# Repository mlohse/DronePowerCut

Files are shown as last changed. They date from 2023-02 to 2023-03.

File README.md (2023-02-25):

# DronePowerCut

This board is supposed to be connected between the main battery and the flight controller of a drone/opto-copter and provides an emergency power-off in case the drone get's out of control.
The board has been designed for 6s LiPo batteries (22.2V) and can handle continuous currents of up to 80A.

# Bill of Material (BOM)
The PCB can be ordered at OSH Park (they ship worldwide):

* https://oshpark.com/shared_projects/SKaDHxAu (rev.A)

It doesn't really matter of which brand/type you order resistors and capacitors, nor does this board require any tight tolerances. You can purchase whatever your local hardware dealer has on stock fitting the value/package described by the schematic.
However, for convenience I've created a virtual shopping basket at Reichelt Elektronik:

* https://www.reichelt.de/my/2021258

MosFETs and Voltage regulator are available at Farnell:

* https://de.farnell.com/infineon/auirfs8409-7trl/mosfet-n-kanal-40v-240a-to-263/dp/2839427?st=auirfs8409
* https://de.farnell.com/microchip/mic5219-3-6ym5-tr/ldo-0-5vdo-0-5a-3-6v-1-5sot23/dp/2510256?st=mic5219

# Building and Flashing the Firmware
You need to have an AVR toolchain installed (make, gcc, binutils)

On Arch Linux simply install the following packages:

`# pacman -S community/avr-gcc community/avr-binutils community/avr-libc`

You may likely want to install avrdude (of course if your programmer requires a different software you can skip this step):

`# pacman -S avrdude`

Please don't forget to adapt the `PROGRAMMER`/`PORT` section in the `Makefile` according to your programmer.

To build the firmware change into the `src` directory and run:

`# make`

...then connect the board to your ISP programmer - the boards needs to be powered (consumes < 50mA) through the programmer - and flash the firmware:

`# make program`

**Optional**: It shouldn't be necessary to flash fuses, as they are left to defaults. But in case the MCU behaves weird in any way...

`# make fuses`

Done.

# LED States (Debugging)

## Power LED (blue)
This led should always be flashing with 1Hz during opartion. If constantly lid or off the MCU has crashed - should never happen of course ;)

## Activity LED (green)
This led indicated whether there is a signal from the receiver:

* **off**: no signal
* **flashing with 5Hz**: invalid signal (pulse to short/long, see `CTRL_DECODER_VAL_MIN`/`CTRL_DECODER_VAL_MAX`)
* **constantly lid**: signal ok (during normal operation this should always be the case)

## OFF LED (red)
This led indicates when lid that power has been cut (emergency off active).

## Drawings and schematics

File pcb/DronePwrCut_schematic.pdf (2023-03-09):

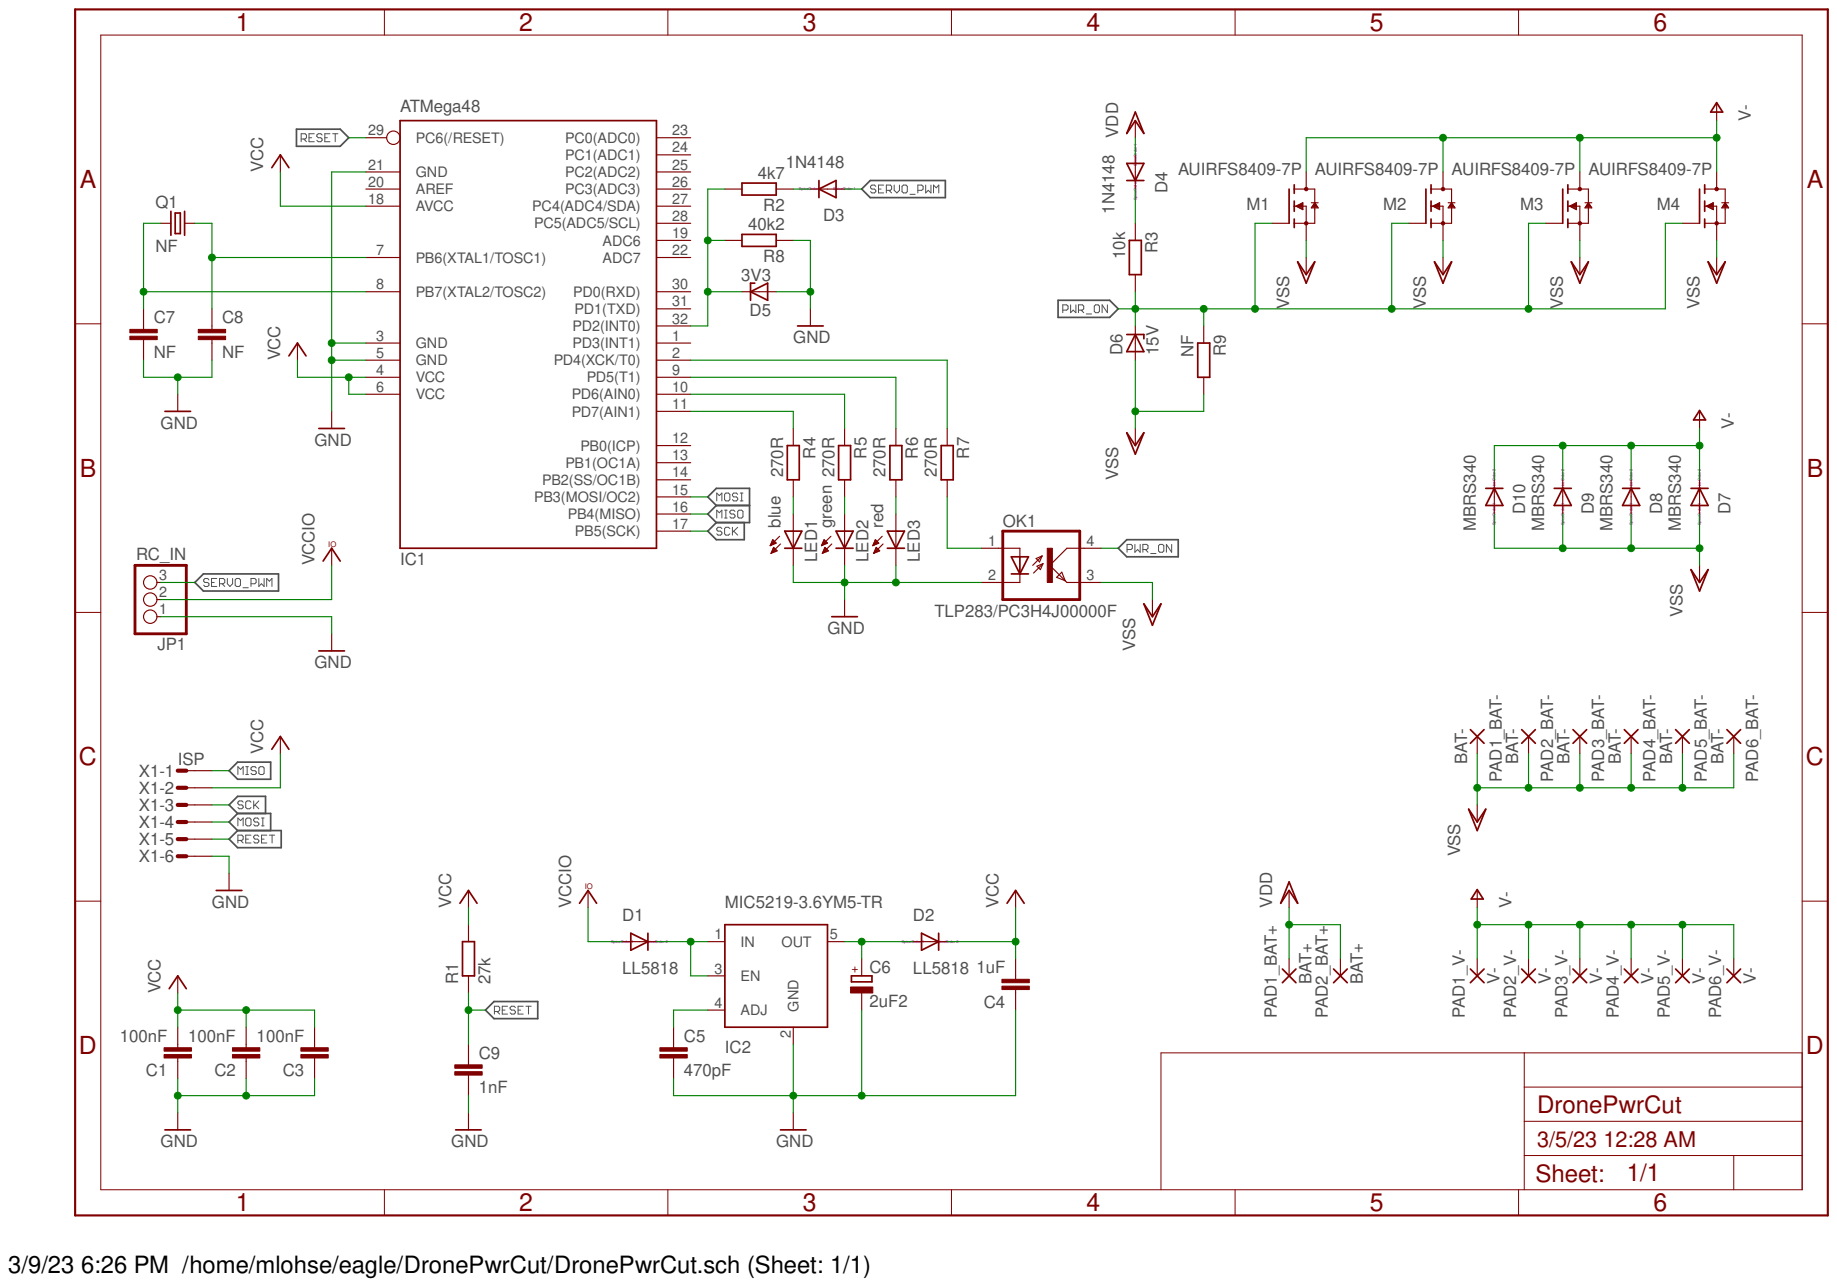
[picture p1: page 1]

BAT- BAT-

3/9/23 6:26 PM /home/mlohse/eagle/DronePwrCut/DronePwrCut.sch (Sheet: 1/1)

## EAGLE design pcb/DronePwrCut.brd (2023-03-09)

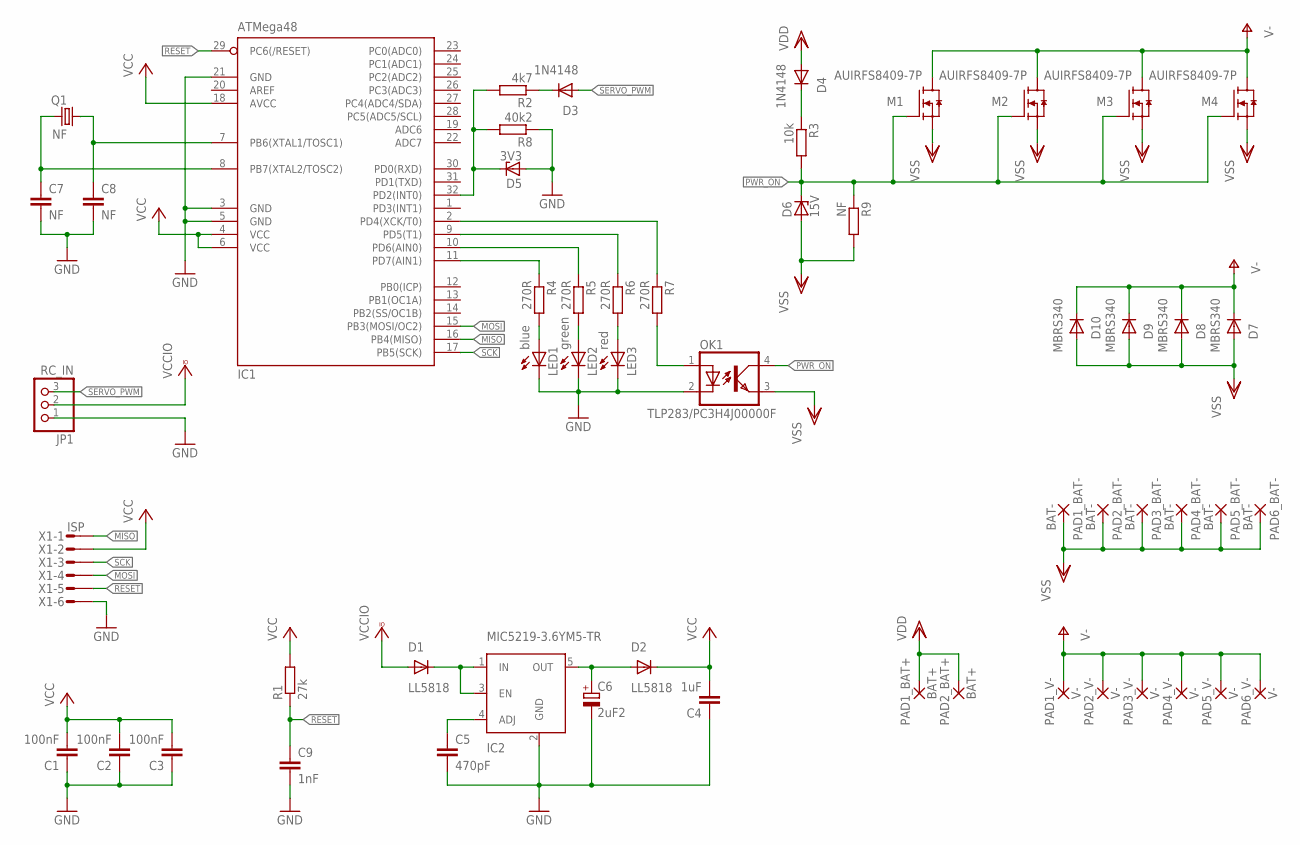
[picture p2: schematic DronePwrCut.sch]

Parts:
C1, C2, C3: 100nF; C1206K
C4: 1uF; C1206K
C5: 470pF; C1206K
C6: 2uF2; SMC_B
C7, C8: NF; C1206K
C9: 1nF; C1206K
D1, D2: LL5818; MELF-MLL41
D3, D4: 1N4148; SOD80C
D5: 3V3; SOD80C
D6: 15V; SOD80C
D7, D8, D9, D10: MBRS340; SMC
IC1: ATMega48; TQFP32-08
IC2: MIC5219-3.6YM5-TR; SOT23-5
JP1: RC_IN; 1X03
LED1: blue; CHIPLED_1206
LED2: green; CHIPLED_1206
LED3: red; CHIPLED_1206
M1, M2, M3, M4: AUIRFS8409-7P; P-TO263-7-1
OK1: TLP283/PC3H4J00000F; MINI-FLAT-4
PAD1_BAT+, PAD2_BAT+: BAT+; 1,6/0,8
PAD1_BAT-, PAD2_BAT-, PAD3_BAT-, PAD4_BAT-, PAD5_BAT-, PAD6_BAT-: BAT-; 1,6/0,8
PAD1_V-, PAD2_V-, PAD3_V-, PAD4_V-, PAD5_V-, PAD6_V-: V-; 1,6/0,8
Q1: NF; HC49UP
R1: 27k; R1206
R2: 4k7; R1206
R3: 10k; R1206
R4, R5, R6, R7: 270R; R1206
R8: 40k2; R1206
R9: NF; R1206
X1: ISP; MICROMATCH-6

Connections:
GND: C1.1, C2.1, C3.1, C4.1, C5.2, C6.-, C7.2, C8.2, C9.2, D5.A, IC1.3 (GND), IC1.5 (GND), IC1.21 (GND), IC2.2 (GND), JP1.1, LED1.C, LED2.C, LED3.C, OK1.2 (C), R8.1, X1.6
MISO: IC1.16 (PB4(MISO)), X1.1
MOSI: IC1.15 (PB3(MOSI/OC2)), X1.4
unnamed: C8.1, IC1.7 (PB6(XTAL1/TOSC1)), Q1.1
unnamed: C6.+, D2.A, IC2.5 (OUT)
unnamed: C5.1, IC2.4 (ADJ)
unnamed: D1.C, IC2.1 (IN), IC2.3 (EN)
unnamed: C7.1, IC1.8 (PB7(XTAL2/TOSC2)), Q1.2
unnamed: D5.C, IC1.32 (PD2(INT0)), R2.2, R8.2
unnamed: D3.C, R2.1
unnamed: D4.C, R3.1
unnamed: IC1.11 (PD7(AIN1)), R4.1
unnamed: IC1.10 (PD6(AIN0)), R5.1
unnamed: IC1.9 (PD5(T1)), R6.1
unnamed: IC1.2 (PD4(XCK/T0)), R7.1
unnamed: LED1.A, R4.2
unnamed: LED2.A, R5.2
unnamed: LED3.A, R6.2
unnamed: OK1.1 (A), R7.2
PWR_ON: D6.C, M1.1 (G), M2.1 (G), M3.1 (G), M4.1 (G), OK1.4 (COL), R3.2, R9.1
RESET: C9.1, IC1.29 (PC6(/RESET)), R1.1, X1.5
SCK: IC1.17 (PB5(SCK)), X1.3
SERVO_PWM: D3.A, JP1.3
V-: D7.C, D8.C, D9.C, D10.C, M1.7 (D), M2.7 (D), M3.7 (D), M4.7 (D), PAD1_V-.1, PAD2_V-.1, PAD3_V-.1, PAD4_V-.1, PAD5_V-.1, PAD6_V-.1
VCC: C1.2, C2.2, C3.2, C4.2, D2.C, IC1.4 (VCC), IC1.6 (VCC), IC1.18 (AVCC), R1.2, X1.2
VCCIO: D1.A, JP1.2
VDD: D4.A, PAD1_BAT+.1, PAD2_BAT+.1
VSS: D6.A, D7.A, D8.A, D9.A, D10.A, M1.2 (S), M1.3 (S), M1.4 (S), M1.5 (S), M1.6 (S), M2.2 (S), M2.3 (S), M2.4 (S), M2.5 (S), M2.6 (S), M3.2 (S), M3.3 (S), M3.4 (S), M3.5 (S), M3.6 (S), M4.2 (S), M4.3 (S), M4.4 (S), M4.5 (S), M4.6 (S), OK1.3 (EMIT), PAD1_BAT-.1, PAD2_BAT-.1, PAD3_BAT-.1, PAD4_BAT-.1, PAD5_BAT-.1, PAD6_BAT-.1, R9.2

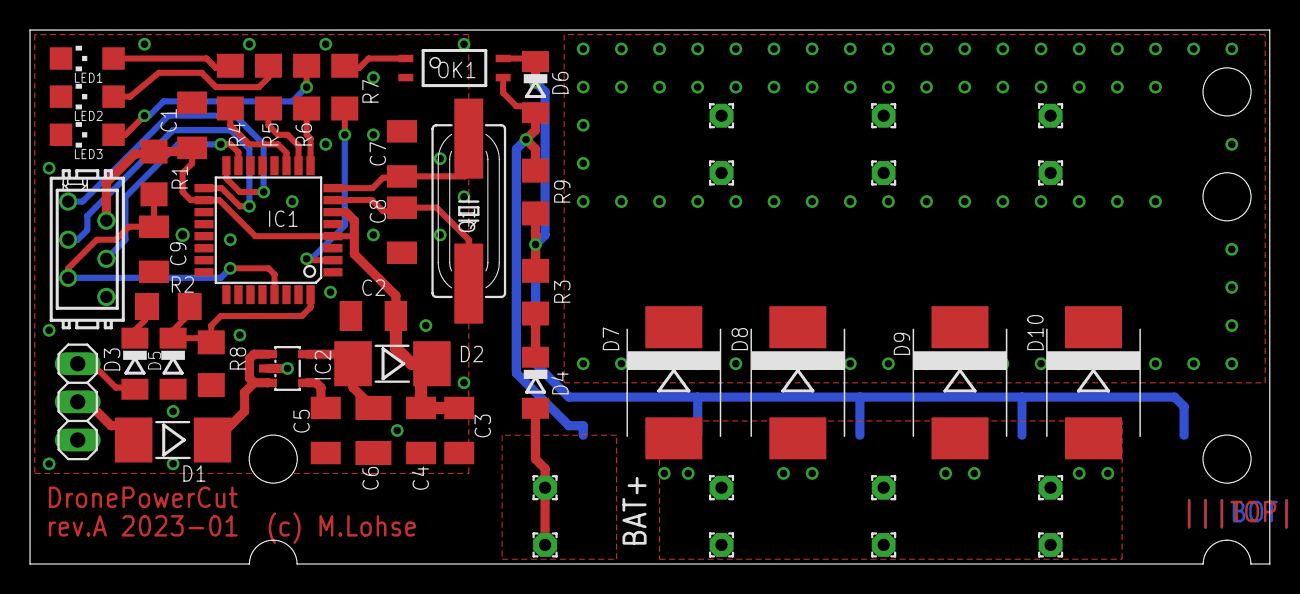
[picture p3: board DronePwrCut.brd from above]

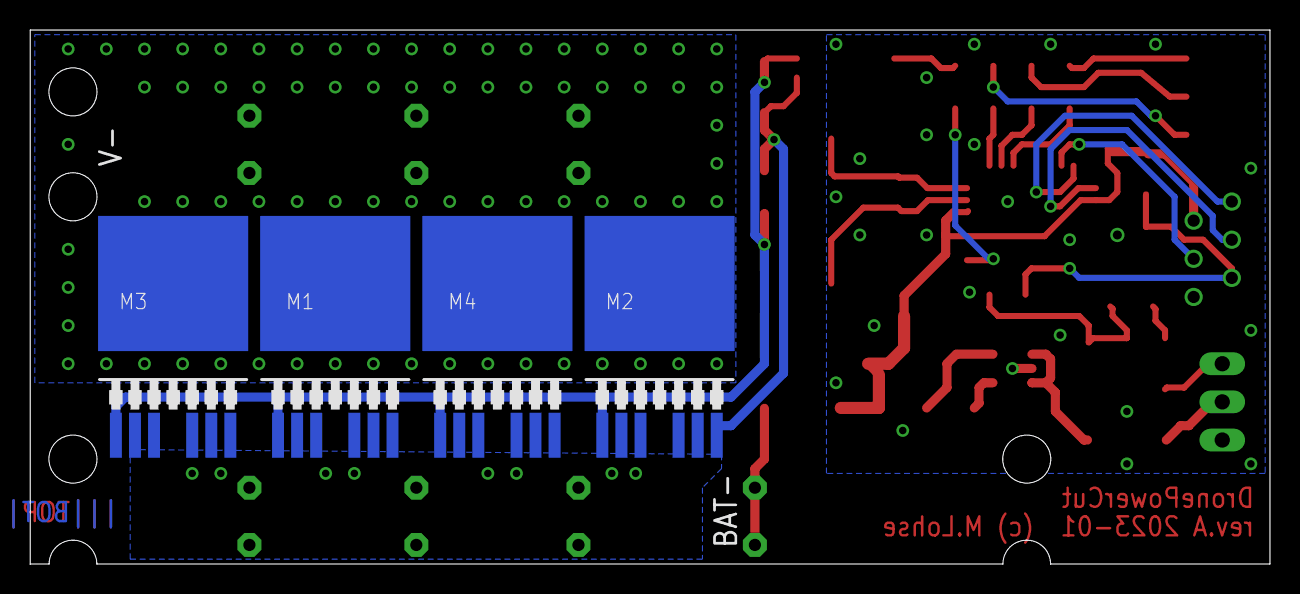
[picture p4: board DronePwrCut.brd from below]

Board: 2 copper layers, 82.5 x 35.5 mm, 55 parts (4 on the bottom side), 28 nets.

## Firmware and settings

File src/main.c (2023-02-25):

/*******************************************************************************
 * main.c                                                                      *
 * author:  Markus Lohse <mlohse@gmx.net>                                      *
 * date:    2023-02-05                                                         *
 * license: LGPLv3, see https://www.gnu.org/licenses/lgpl-3.0.txt              *
 ******************************************************************************/
#include <avr/io.h>
#include "timer.h"
#include "led.h"
#include "config.h"
#include "decoder.h"
#include "ctrl.h"


static void init(void)
{
	/* configure & initialize io ports */
/*	DDRA = IO_DDRA; -> not available on AtMega48 */
	DDRB = IO_DDRB;
	DDRC = IO_DDRC;
	DDRD = IO_DDRD;
	
/*	PORTA = INIT_PORTA; -> not available on AtMega48 */
	PORTB = INIT_PORTB;
	PORTC = INIT_PORTC;
	PORTD = INIT_PORTD;

	timer_init();
/*	led_flash();*/
	decoder_init();
	ctrl_init();
}

int main(void)
{
	init();

	while(1)
	{
		/* insert main code here */
		led_set(LED_PWR, (timer_uptime() % MAIN_INTVAL_PWR) < (MAIN_INTVAL_PWR / 2));
		ctrl_run();
	}
}

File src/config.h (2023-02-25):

/*******************************************************************************
 * Config file for Drone Power Cut board rev. A                                *
 * author:  Markus Lohse <mlohse@gmx.net>                                      *
 * date:    2023-02-05                                                         *
 * license: LGPLv3, see https://www.gnu.org/licenses/lgpl-3.0.txt              *
 ******************************************************************************/
#ifndef CONFIG_H_
#define CONFIG_H_

#define BOARD_REV_A

/***********************************
 * IO Ports                        *
 ***********************************/
//#define IO_DDRA               0xFF    // -> not available on AtMega48!
#define IO_DDRB                 0xC7    // PortB [0..4] unused out, 3 mosi input, 4 miso input, 5 sck input
#define IO_DDRC                 0xFF    // PortC [0..6] unused out, 7 switch out
#define IO_DDRD                 0xFB    // PortD [0,1,3] unused out, 2 servo in, 4 opto-coupler out, [5..7] LED1-3 out

/* led definition for led.h */
#define PORT_LED0               PORTD
#define PORT_LED1               PORTD
#define PORT_LED2               PORTD
#define PORT_LED3               PORTD

#define PIN_LED0                4       // opto-coupler out (LED_PWR)
#define PIN_LED1                5       // red
#define PIN_LED2                6       // green
#define PIN_LED3                7       // blue

#define LED_NUM                 4

/* led names to be used with led_on, led_off,... */
#define LED_OPT                 0
#define LED_PWR                 3
#define LED_ACT                 2
#define LED_OFF                 1


/***********************************
 * Initialization                  *
 ***********************************/
//#define INIT_PORTA              0x00  // -> not available on AtMega48!
#define INIT_PORTB              0x38    // pull unused pins to GND, enable pullups for mosi/miso/sck
#define INIT_PORTC              0x00    // pull unused pins to GND
#define INIT_PORTD              0x00    // pull unused pins to GND, switch off leds, disable pullups


/***********************************
 * Servo decoder                   *
 ***********************************/
#define DECODER_INPUT_PORT      PIND    // Port for servo signal to be decoded
#define DECODER_INPUT_PIN       2       // Pin for servo signal
#define DECODER_TIMEOUT_NOSIG   25000   // timeout (us) for reporting "no signal" -> min 40Hz


/***********************************
 * Controller                      *
 ***********************************/
#define CTRL_DECODER_VAL_MIN    750     // min signal length (usec) before signal is being markes as invalid
#define CTRL_DECODER_VAL_MAX    2250    // max signal length (usec) before signal is being markes as invalid
#define CTRL_DECODER_VAL_TRIG   1500    // signal length (usec) triggering power on/off
#define CTRL_DECODER_INVERT     0       // if set '1' on/off states will be inverted
#define CTRL_DELAY_PWR_ON       1500    // 1.5 sec delay before power is restored (should be long enough to ensure that MosFETs do not overheat!)
#define CTRL_DELAY_PWR_OFF      200     // 0.2sec delay before power is cut (~10 pulses)
#define CTRL_INTVAL_INVALID_SIG 200     // interval in msec -> flash act led 5Hz when receiver signal is invalid


/***********************************
 * MAIN                            *
 ***********************************/
#define MAIN_INTVAL_PWR         1000    // interval in msec -> flash pwr led 1Hz

#endif /* CONFIG_H_ */

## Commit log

2023-02-25 initial version
    [DronePwrCut.brd, DronePwrCut.sch]
2023-02-25 add section led states
2023-03-09 Change resistor values (R2, R8) to handle low voltage (3V3) input signals correctly
    [DronePwrCut.sch]
